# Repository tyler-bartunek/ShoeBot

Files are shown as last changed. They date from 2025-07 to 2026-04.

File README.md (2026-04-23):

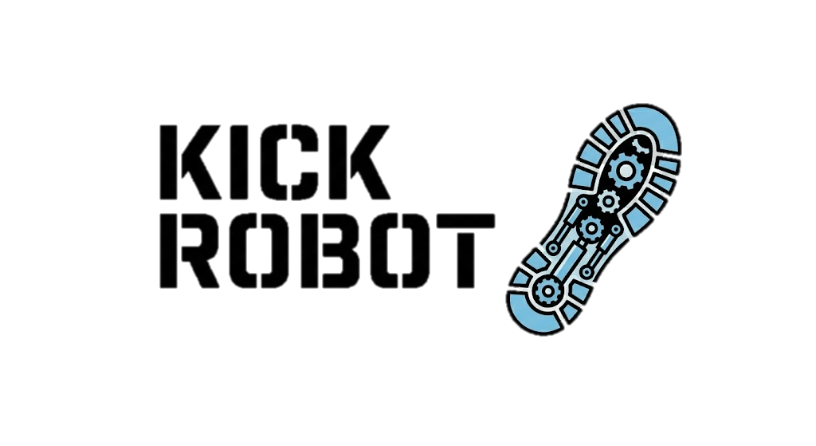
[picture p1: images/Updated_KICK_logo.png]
KICK Logo
# The KICK Robot 

&nbsp;
&nbsp;
_Democratizing robotics, one shoebox at a time_

The KICK (Kinematically Interchangeable Control Kit) Robot framework is an open-source platform designed to make learning about and development of mobile robotic systems accessible, modular, and affordable.

## Table of Contents
- [Repository Structure](#repository-structure)
- [The Wiki](#the-wiki)
- [Module Descriptions](#module-descriptions)
- [Hardware](#hardware)
  - [Printed Components and Module Fit](#printed-components-and-module-fit)
- [Future development](#future-development)
- [FAQ](#faq)
- [License](#license)

## Repository Structure
- `/hardware/` – STL and STEP files for 3D printing
- `/software/` – Code for the centralized controller (in progress), example firmware for modules, and hardware test scripts
- `/docs/` – Printing instructions, and additional reference material as it becomes available (PDF)
- `/images/` – Holds images used in this README, as well as some others throughout the repository
- `README.md` – You are here.

## The Wiki
Documentation for this project, including: 

- Part orientation and printer setting recommendations
- Assembly instructions
- Calibration and hardware validation protocols
- System-level descriptions
- and more

are being migrated to the [project wiki](https://www.github.com/tyler-bartunek/KICK-Robot/wiki) for ease of access
and navigation purposes. There's a lot that goes into this system, and it is only fitting that worthy documentation
would be quite extensive, requiring a wiki to track it all. 

## Module Descriptions
Here are a few of the modules under development at present for the KICK Robot. Once these modules are fully fleshed
out, a homebrew guide will be produced and added to the wiki.

1. Wheels: This module consists of DC motors and mecanum wheels, represents minimal functional example (systems integration in process).
2. Shoeshine: Offers quadrupedal motion through use of servomotors (Pending Initial Design)
3. HexaBox: Requires six mounts, offers six-legged locomotion through use of servomotors. (Pending Initial Design)

## Hardware

### Printed Components and Module Fit
Both STEP and STL files for all components to be printed are provided under the hardware directory, with directions for
the base hardware and wheels module provided in the wiki. As modules are added, printing directions specific
to those modules will be added. This system was prototyped using an Ender 3 V2 and Cura slicer using 
PLA+, with dimensions set to reflect typical tolerances for that printer with the intent of clearance fits with minimal play between 
mounting rails and modules.

## Future development
This project is still under development, and additional details such as component IDs, synchronization, and timing
requirements will be made available as they are validated 

## FAQ

1. Why shoeboxes?

>I had originally set out to make what essentially amounts to just the wheels module as a CAD and mechatronic portfolio piece.
Seeking to understand the design considerations, I started to immerse myself in literature surrounding mecanum wheel devices 
and discovered something that is in hindsight self-evident: different design decisions like the wheel spacing and orientation 
fundamentally alters the dynamics of the system and therefore influence control. Creating modular systems to explore the impact 
of these parameters was largely underexplored in what I found, so I set out to make my own. But I needed a good frame. Something
cheap and easy to deploy. As I looked around me, I saw an unused shoebox. And the KICK Robot was born. 

>Realistically any cardboard box will work, but at the time a shoebox seemed like the right size for what I set out to accomplish.

2. Why didn't you use \<insert fastener here\> to fasten the modules to the box?

>In the early days, I explored a number of different means for mounting the hardware to the box. The current design for mounting
hardware to the box solves two problems simultaneously: the first is that of establishing a secure connection with minimal
assembly complexity, the second is offering a path for routing the wires from inside the box to the modules on the outside.

3. Doesn't the act of cutting into the box limit the reusability of a single box to test multiple design parameters?

>Yes, as do other adhesives that have enough strength to reliably anchor the hardware to the outside of the box. 

## License
As of 19 November, 2025, this project is licensed under the terms of the [Apache License-2.0](LICENSE). Software provided prior 
to this date was licensed under the terms of the MIT license, and includes the content of the directory 
`/software/Hardware Characterization/Wheels Module`. The transition to the Apache License-2.0 is to reflect that this repository
contains more than just software. 

This project also uses PyMC in the motor characterization code for the Wheels module. PyMC is also licensed under the terms
of the [Apache License-2.0](LICENSE), and also includes software licensed under the MIT license. A notice is provided in the
main directory of this repository, to underline this point and include the necessary copy of the MIT license for portions 
covered by that license.

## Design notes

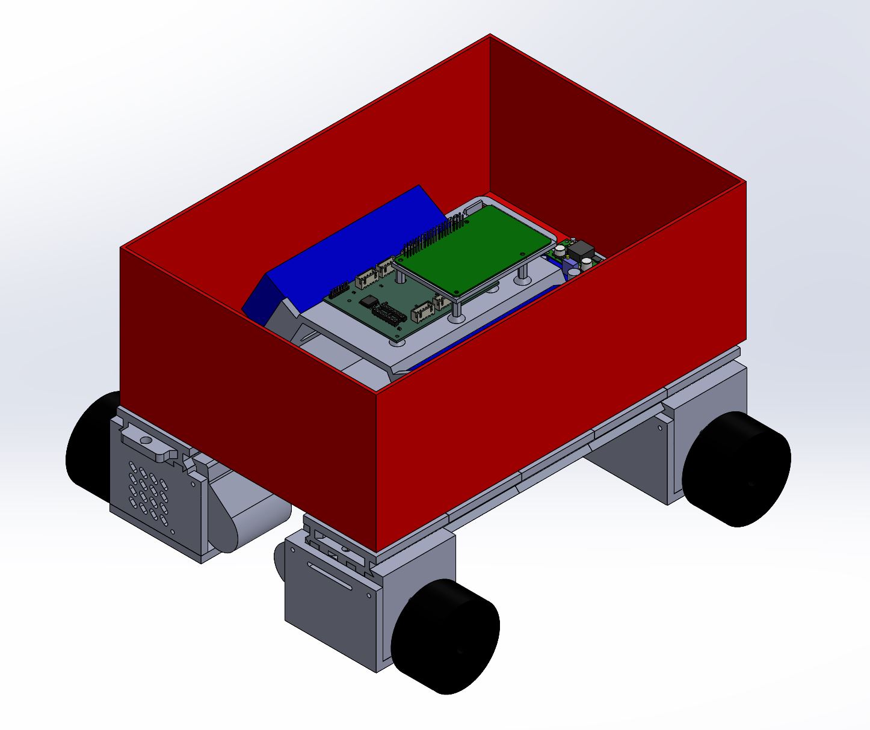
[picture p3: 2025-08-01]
images/ShoeBot_Wheels_Render_Iso.JPG

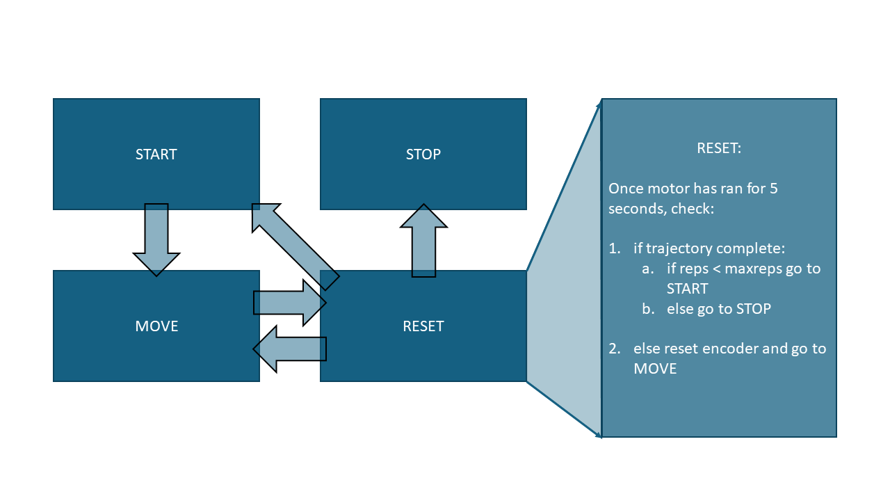
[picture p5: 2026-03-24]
images/wiki/MotorStateMachine.png

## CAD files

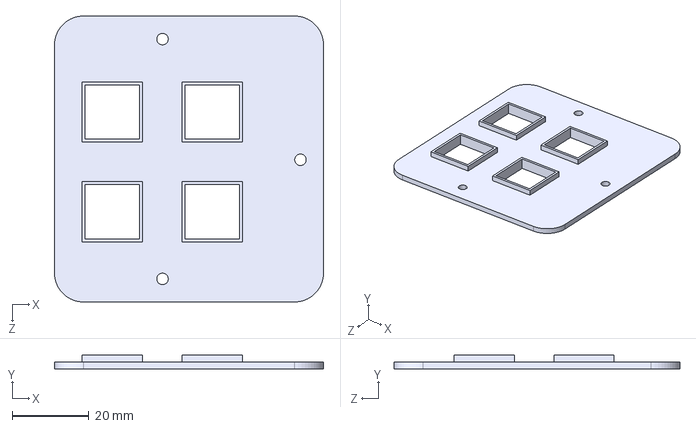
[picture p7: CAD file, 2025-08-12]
Hardware/Attachment Points/STEPs/BasePlate_Ext_Middle.STEP
70.0 x 3.60 x 74.4 mm

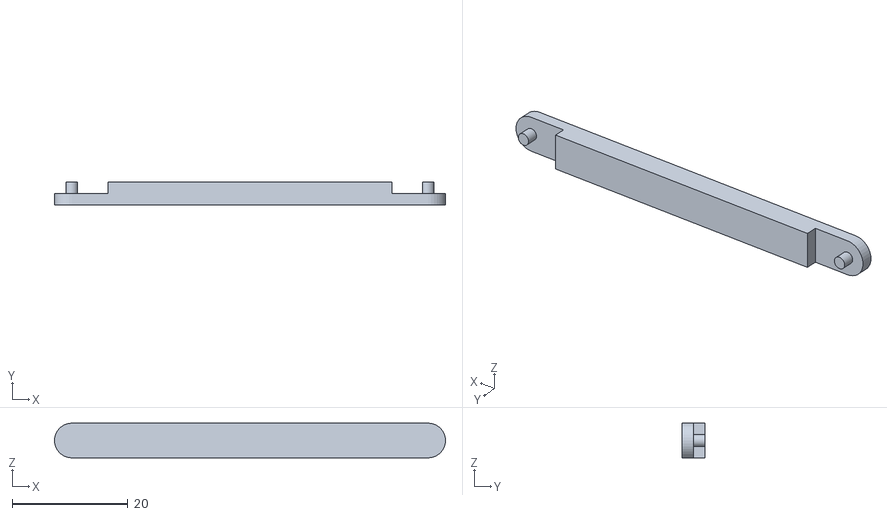
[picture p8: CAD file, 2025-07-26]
Hardware/Attachment Points/STLs/PlateSpacer.STL
67.5 x 4.00 x 6.00

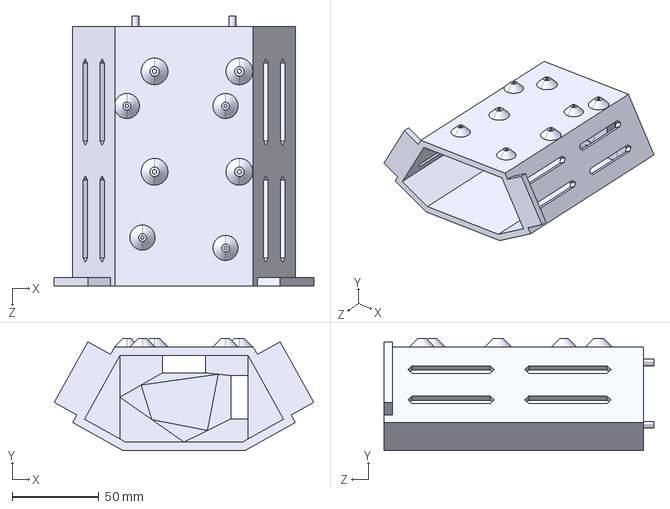
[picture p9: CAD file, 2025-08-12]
Hardware/Central Electronic Mounts/STEPs/Central_Electronics_Mount.STEP
150.0 x 65.0 x 156.0 mm

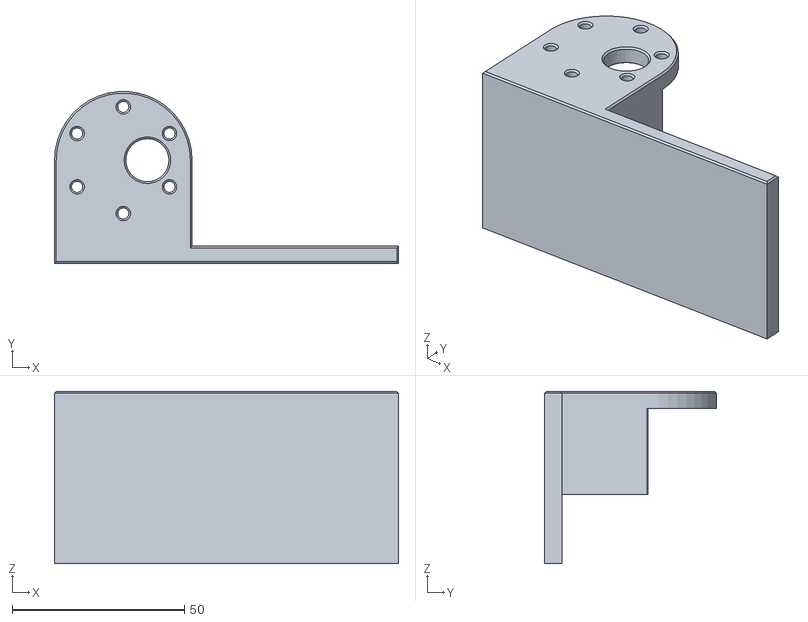
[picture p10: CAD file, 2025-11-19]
Hardware/Wheel Module/Motor Characterizetion STL/MotorWheel_Characterization.STL
100.0 x 49.9 x 50.0

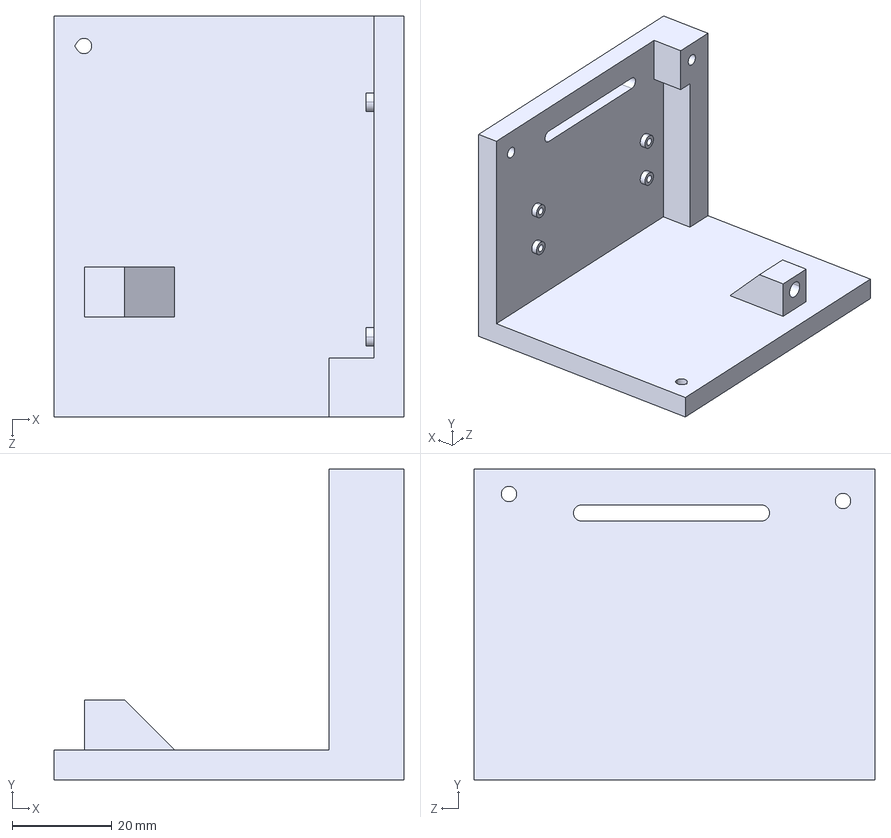
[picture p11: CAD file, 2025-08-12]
Hardware/Wheel Module/STEPs/Motor_Mount_Side_Bottom.STEP
70.0 x 62.2 x 80.2 mm

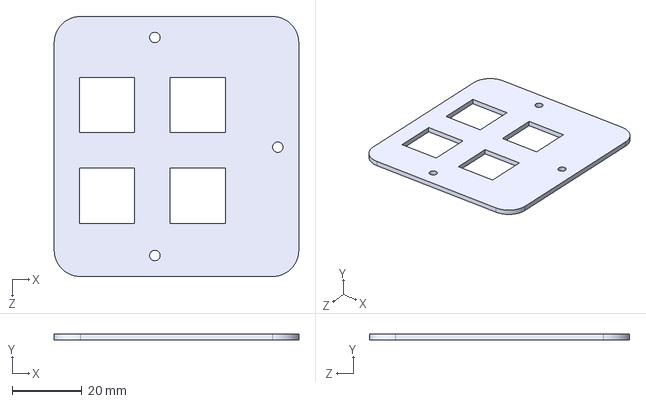
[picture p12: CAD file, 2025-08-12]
Hardware/Attachment Points/STEPs/BasePlate_Int_Middle.STEP
70.0 x 1.80 x 74.4 mm

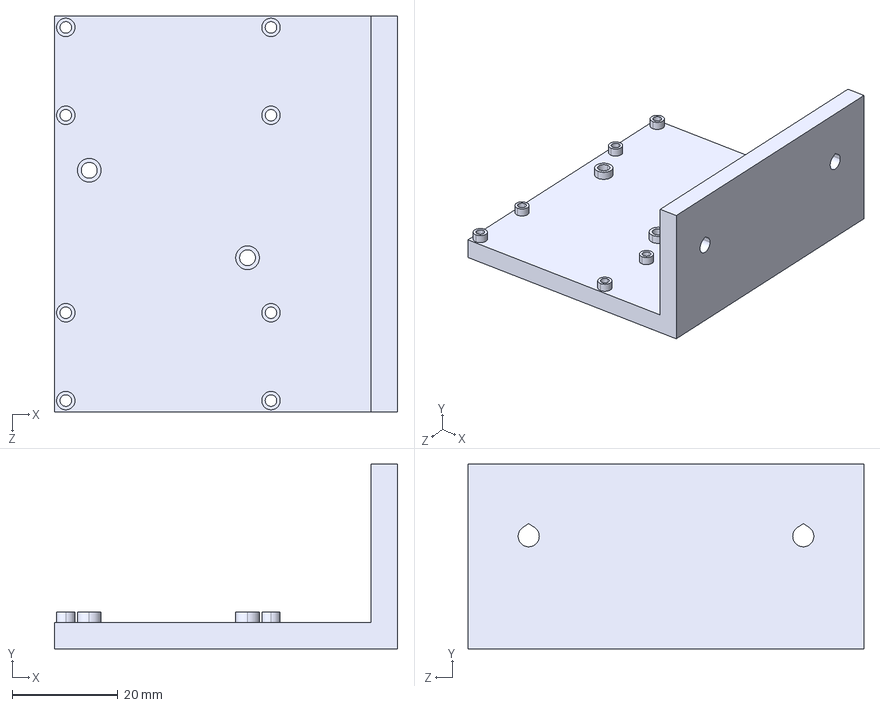
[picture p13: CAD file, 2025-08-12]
Hardware/Central Electronic Mounts/STEPs/Buck_Mount.STEP
65.0 x 35.0 x 75.0 mm

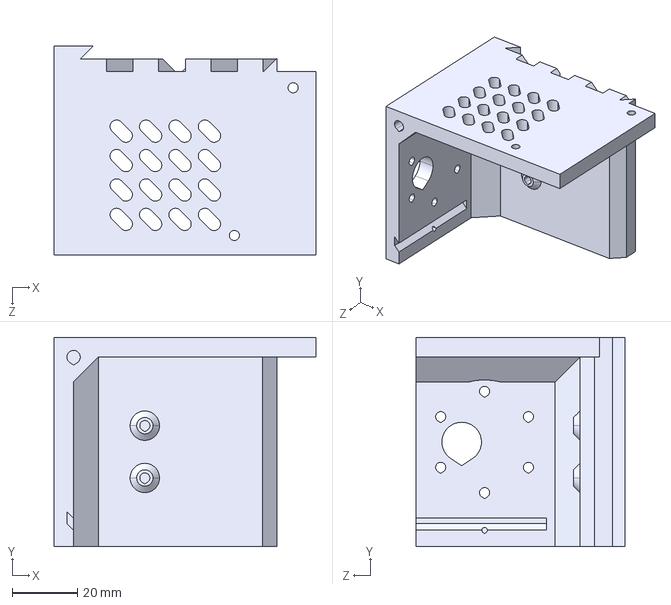
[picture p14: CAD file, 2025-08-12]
Hardware/Wheel Module/STEPs/Motor_Mount_Attachment.STEP
80.2 x 64.0 x 64.0 mm

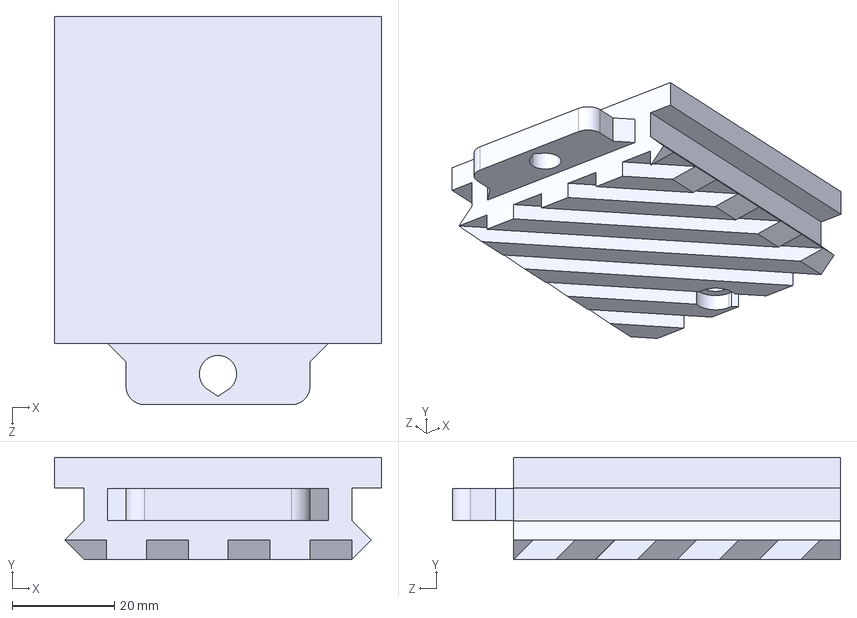
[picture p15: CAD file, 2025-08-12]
Hardware/Attachment Points/STEPs/BaseMount.STEP
64.0 x 20.0 x 76.0 mm

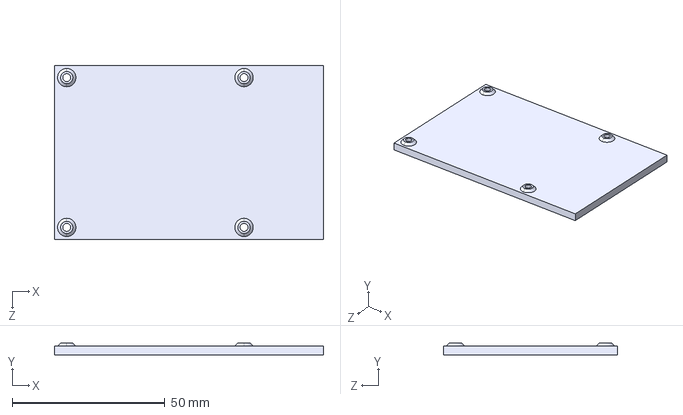
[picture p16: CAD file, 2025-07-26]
Hardware/Central Electronic Mounts/STEPs/Rpi_3b_mount.STEP
88.0 x 4.00 x 57.0 mm

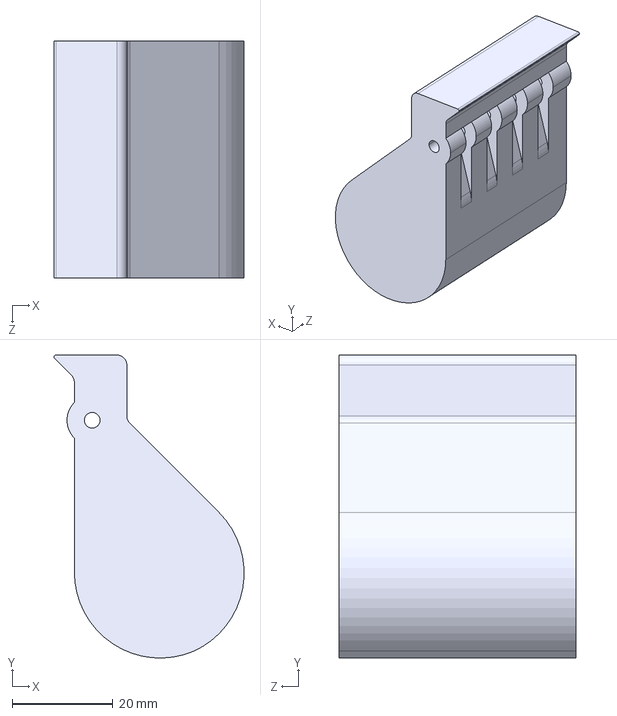
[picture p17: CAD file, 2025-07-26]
Hardware/Wheel Module/STEPs/Handle.STEP
37.6 x 60.1 x 47.0 mm

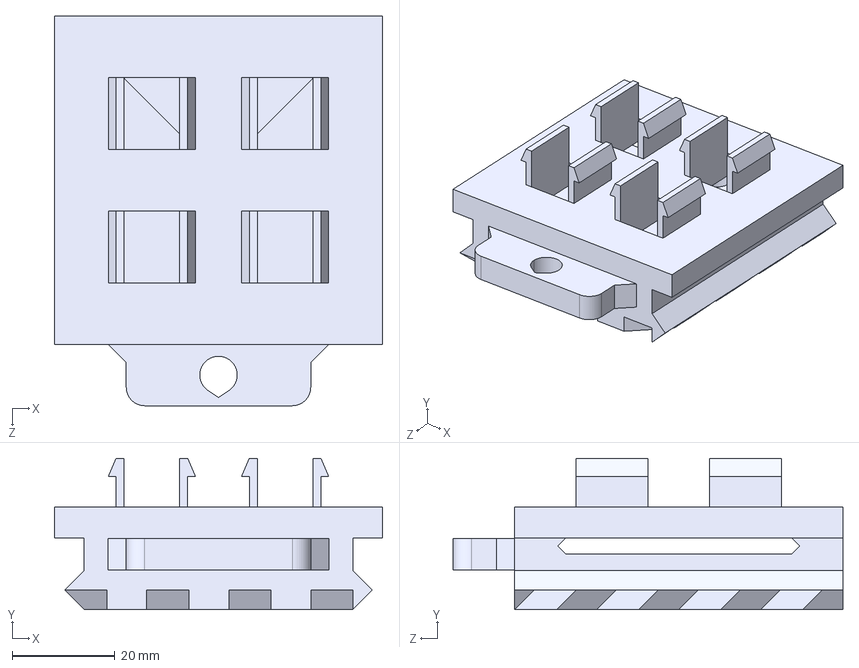
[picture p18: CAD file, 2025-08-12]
Hardware/Attachment Points/STEPs/BaseMount_Clips.STEP
64.0 x 29.5 x 76.0 mm

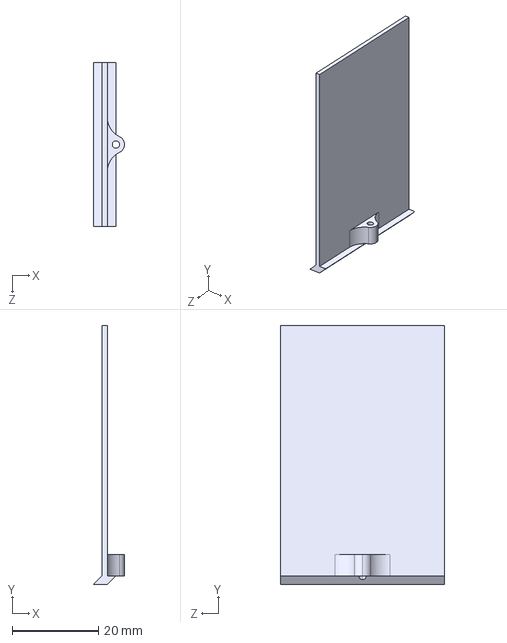
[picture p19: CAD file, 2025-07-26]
Hardware/Wheel Module/STEPs/Pico_Shield.STEP
7.20 x 60.0 x 38.0 mm

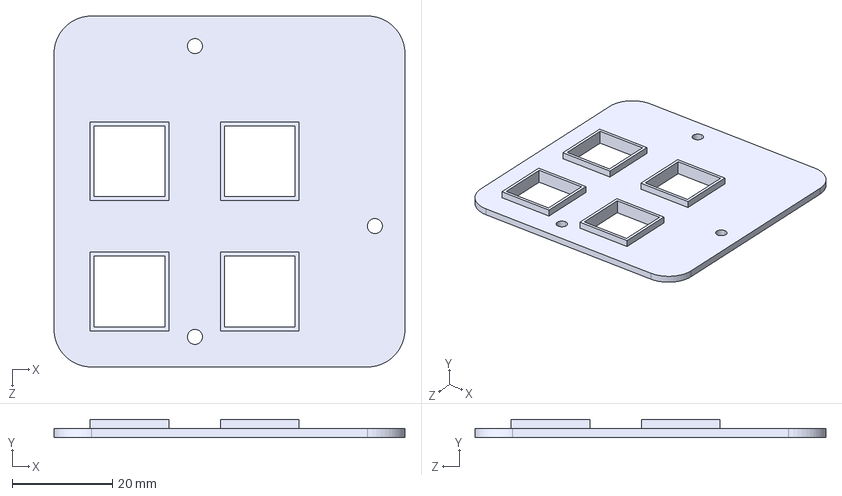
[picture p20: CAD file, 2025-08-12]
Hardware/Attachment Points/STEPs/BasePlate_Ext_Corner.STEP
70.0 x 3.60 x 70.0 mm

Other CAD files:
Hardware/Attachment Points/STEPs/BasePlate_Int_Corner.STEP
Hardware/Attachment Points/STLs/BaseMount.STL
Hardware/Attachment Points/STLs/BaseMount_Clips.STL
Hardware/Attachment Points/STLs/BasePlate_Ext_Corner.STL
Hardware/Attachment Points/STLs/BasePlate_Ext_Middle.STL
Hardware/Attachment Points/STLs/BasePlate_Int_Corner.STL
Hardware/Attachment Points/STLs/BasePlate_Int_Middle.STL
Hardware/Central Electronic Mounts/STLs/Central_Electronics_Mount.STL
Hardware/Central Electronic Mounts/STLs/Rpi_3b_mount.STL
Hardware/Wheel Module/STLs/Handle.STL
Hardware/Wheel Module/STLs/MotorMount_Attachment.STL
Hardware/Wheel Module/STLs/Motor_Mount_Attachment.STL
Hardware/Wheel Module/STLs/Motor_Mount_Side_Bottom.STL
Hardware/Wheel Module/STLs/Pico_Shield.STL

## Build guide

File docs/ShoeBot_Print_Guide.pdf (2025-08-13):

# ShoeBot

# Quick-Start Excerpt: Printing Guide

## Revision Date: August 7, 2025

# Contents

## Downloading Files

These instructions are written for a Windows 10 computer, though the basic principles should transfer reasonably well to other platforms like Mac and Linux operating systems.

## Installing Git

Open a web browser and navigate to https://git-scm.com/ and go to the downloads page. Follow their posted directions, and once installation is complete you will be ready to get started.

## Cloning the Repository

Once git is installed, open a terminal and navigate to the directory where you would like to save the project files. If you know how to do this already, you can skip the steps detailing this process.

### Navigating to Desired Directory using Command Prompt

You do this on Windows by going to the search bar and typing “cmd”, you should see something like the following come up, though the specifics will depend on the software you have installed on your device.

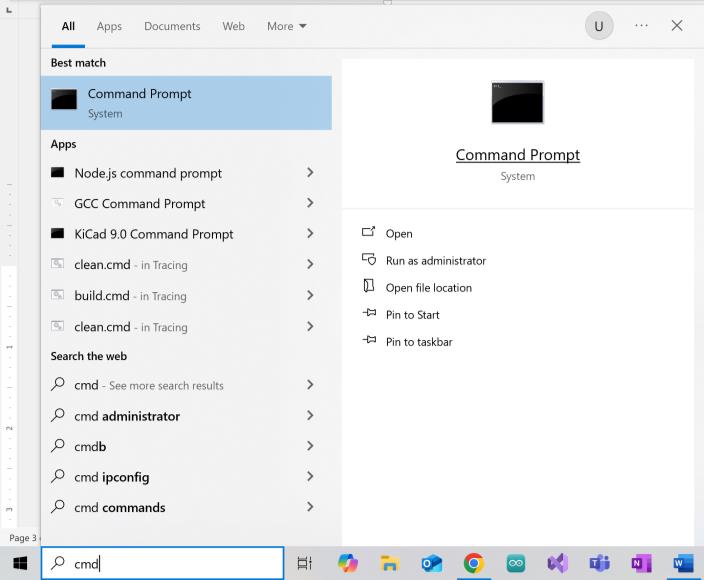
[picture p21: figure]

Figure 1. This screenshot illustrates opening the Command Prompt terminal from the Windows search bar.

1. Open Command Prompt and you should see a terminal window open. Odds are good that your desired location is going to be somewhere off the user directory, which is what Command Prompt opens to by default. In this example, the desired directory is a desktop folder created specifically for the user’s GitHub repositories.

2. Type cd ./<name of target directory> In the example provided in Figure 2, the full command is cd ./Desktop/My Stuffs/Git Repos/

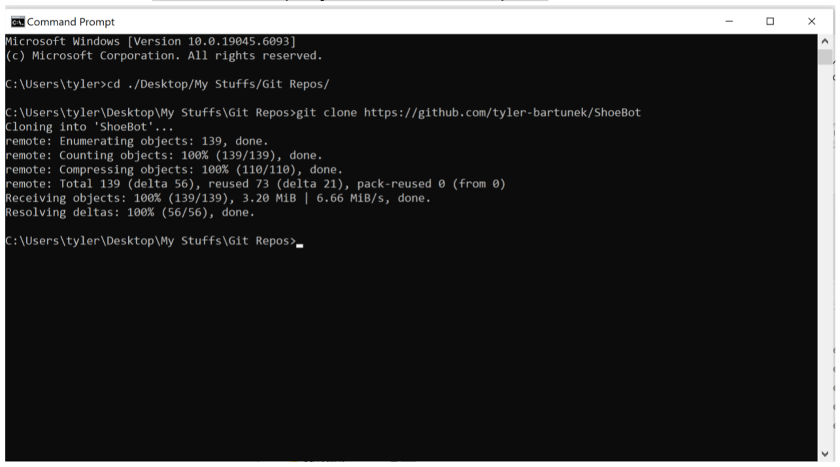
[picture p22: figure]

Figure 2. The complete set of commands necessary to get a clone of the repository onto your local device.

### Finally Cloning the Repository

Now that you are set up with git and are have navigated to the location you want the files to download, it is time to download a copy of the files into this location. Type or copy-paste

git clone https://github.com/tyler-bartunek/ShoeBot

into your terminal. The download process should run automatically and once finished you should have a new folder in that location named ShoeBot. Note that it may prompt you to sign in to github, which may entail setting up an account.

If this step has finished successfully, then you can now close the Command Prompt and continue navigation through the File Explorer like usual.

## Printing Instructions for Hardware

Navigate to the Hardware directory of the repository. In it, you will find folders for

- Attachment Points
- Central Electronic Mounts

- SPI Hub PCB KiCad files
- Wheel Module.

This section will concern all of these folders except the SPI Hub folder, as that information is for an optional component that is not 3D-printed. Every folder that has parts to be 3D-printed will contain folders for STEP and STL files, with the former provided in the event that you need to modify the base design of any of the components.

All parts were printed using PLA+ during the design process with:

- 0.4 mm nozzle and line width
- 20% infill (cubic)
- Tree supports as applicable
- 2 wall lines
- 50 mm/s print speed

To maximize print time efficiency, it is strongly recommended to print multiple components at once. For example, printing half of the rail pieces in a batch and all of the motor mount attachments in another batch instead of each rail and motor mount attachment piece individually. With these print settings it was not uncommon to encounter 2+ day prints on an Ender 3V2 running Marlin. So again, the recommendation is to print as many things simultaneously as possible.

In total, you will need to print the following to match the development setup:

- 6 Base Mount Clips
- 4 Base Mounts
- 4 Internal Corner Plates
- 2 Internal Middle Plates
- 4 External Corner Plates
- 2 External Middle Plates
- 4 Motor Mount Attachments
- 4 Motor Mount Side Bottoms
- 4 Handles
- 4 Pico Shields
- 1 Central Electronics Mount
- 1 Buck Converter Mount
- 1 Raspberry Pi 3b+ Mount
- 4 Spacers (print last)

For best results, print at a 0.1 mm layer height as this will allow in Cura for steeper overhangs and fewer supports.

## Attachment Points

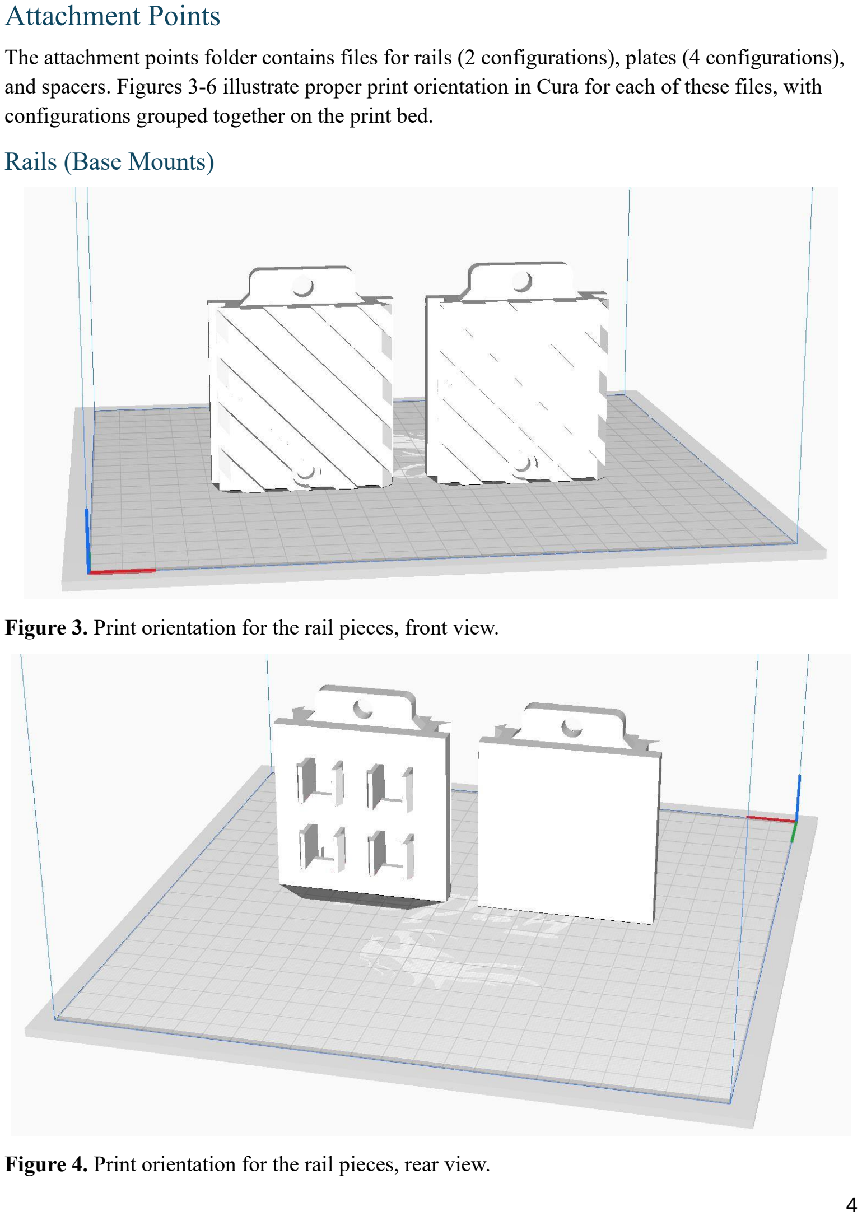
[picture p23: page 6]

The attachment points folder contains files for rails (2 configurations), plates (4 configurations), and spacers. Figures 3-6 illustrate proper print orientation in Cura for each of these files, with configurations grouped together on the print bed.

### Rails (Base Mounts)

Figure 3. Print orientation for the rail pieces, front view.

Figure 4. Print orientation for the rail pieces, rear view.

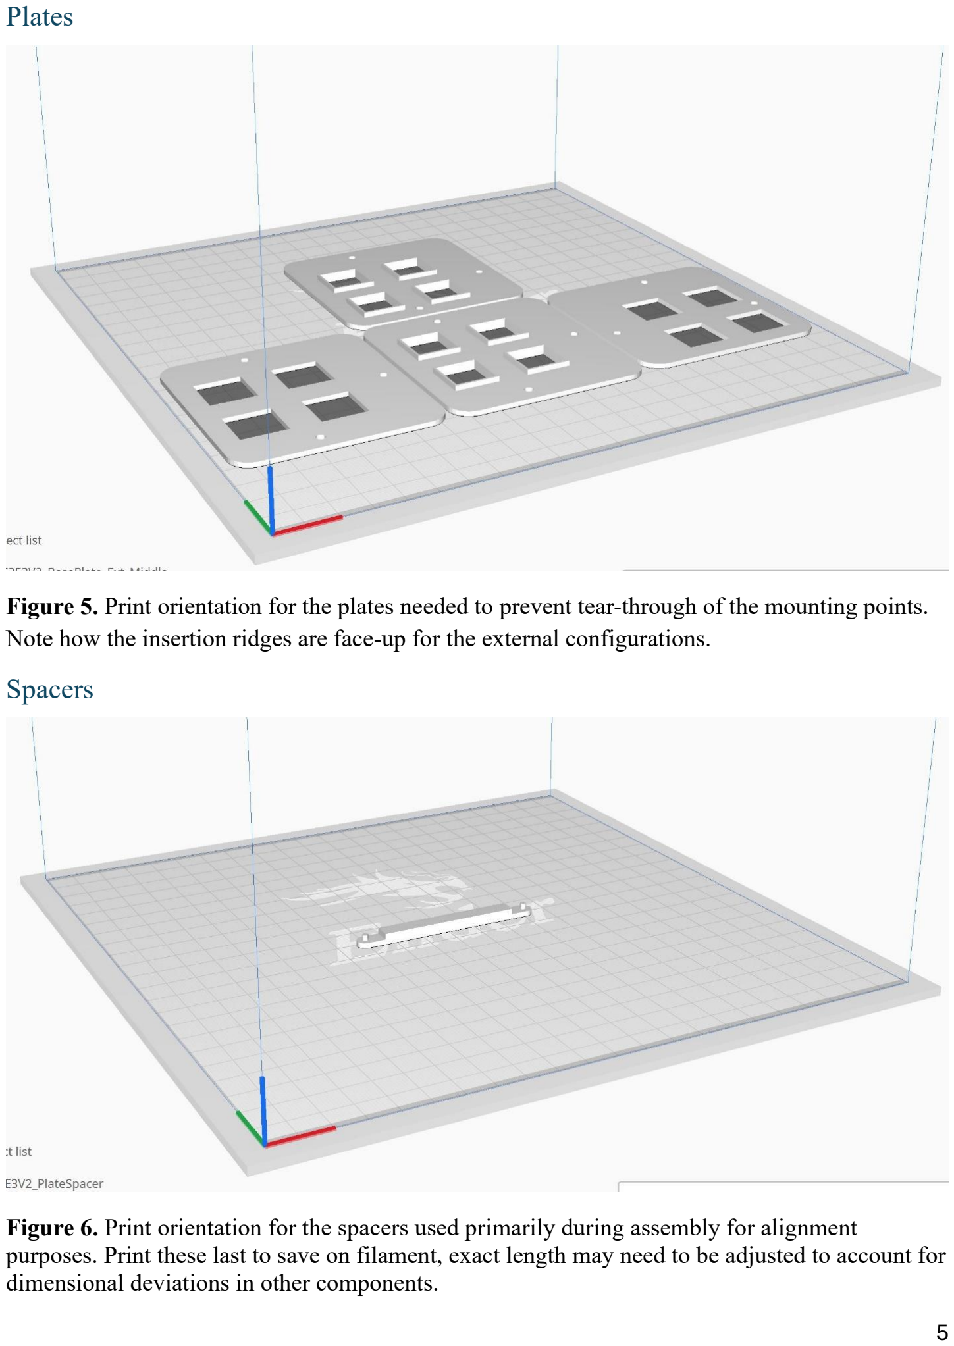
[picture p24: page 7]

### Plates

Figure 5. Print orientation for the plates needed to prevent tear-through of the mounting points. Note how the insertion ridges are face-up for the external configurations.

### Spacers

Figure 6. Print orientation for the spacers used primarily during assembly for alignment purposes. Print these last to save on filament, exact length may need to be adjusted to account for dimensional deviations in other components.

## Central Electronics Mounts

### Raspberry Pi 3B+ Mount

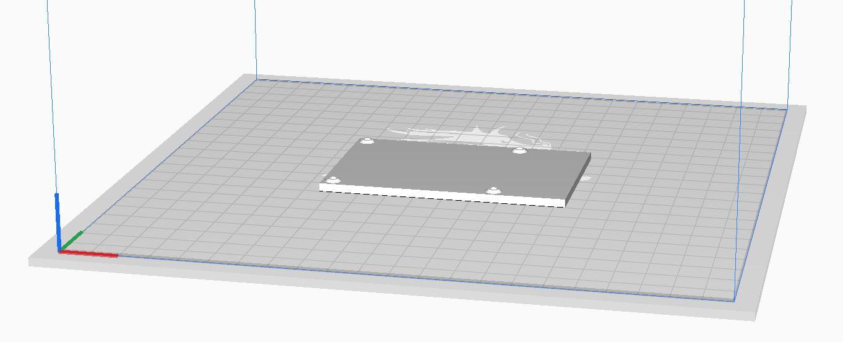
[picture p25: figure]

Figure 7. Print orientation for the plate that the raspberry pi sits upon, with screws going through the pi and this plate into standoffs.

### Central Mount

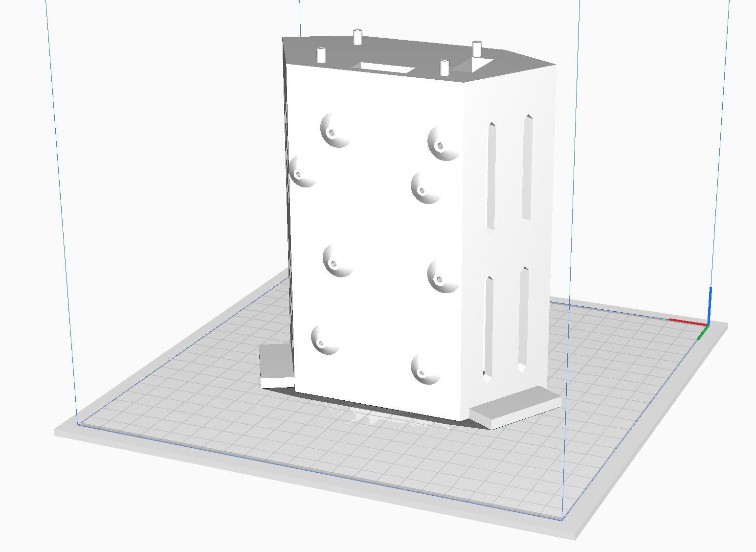
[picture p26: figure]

Figure 8. Print orientation for the central electronics mount. Note that the center of this will be hollow, and you may have to disable supports through part of it in order to improve print times. Small cuts were made in the top of the hollowed out portion to decrease the bridging distance to always be less than 50 mm.

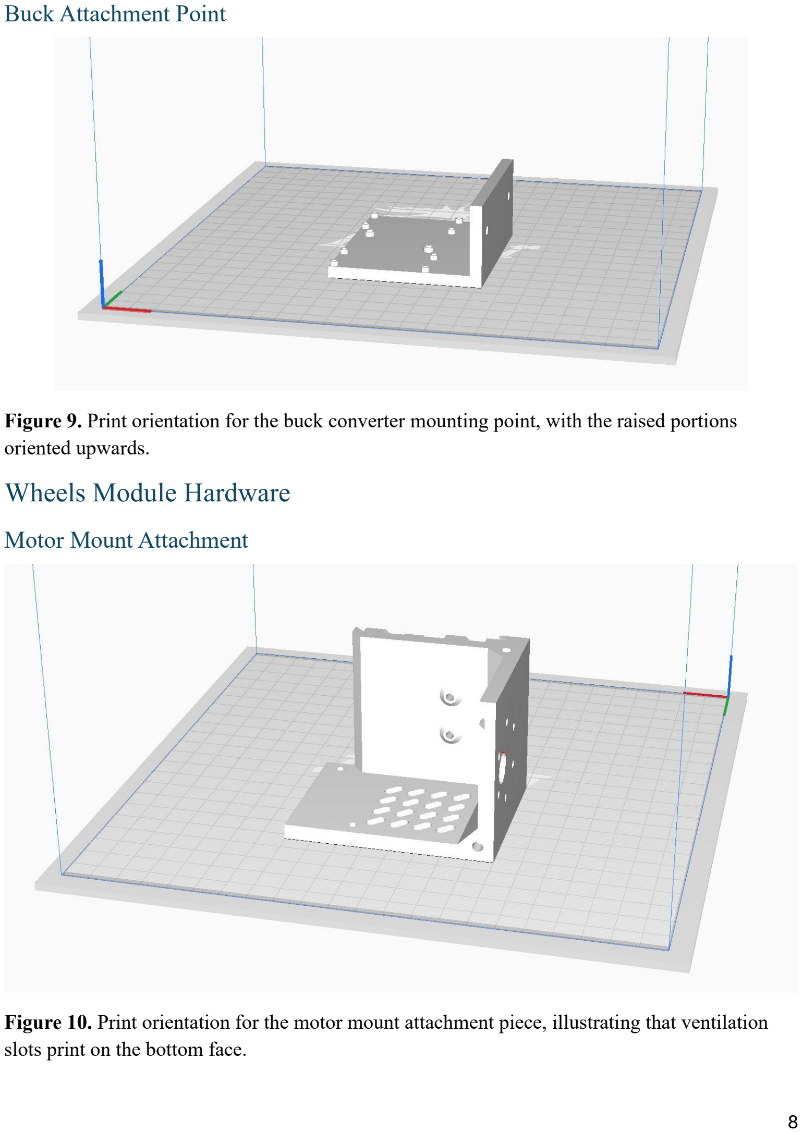
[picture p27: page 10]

### Buck Attachment Point

Figure 9. Print orientation for the buck converter mounting point, with the raised portions oriented upwards.

## Wheels Module Hardware

### Motor Mount Attachment

Figure 10. Print orientation for the motor mount attachment piece, illustrating that ventilation slots print on the bottom face.

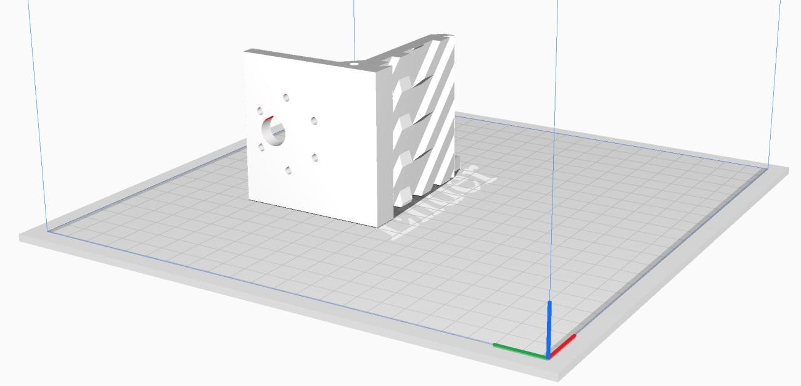
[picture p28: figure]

Figure 11. Secondary view of the print orientation for the motor mount attachment piece, showing that the teardrop shape for the motor attachment holes point upward and the way that the channels should appear in the correct print orientation.

### Motor Mount Side Bottom

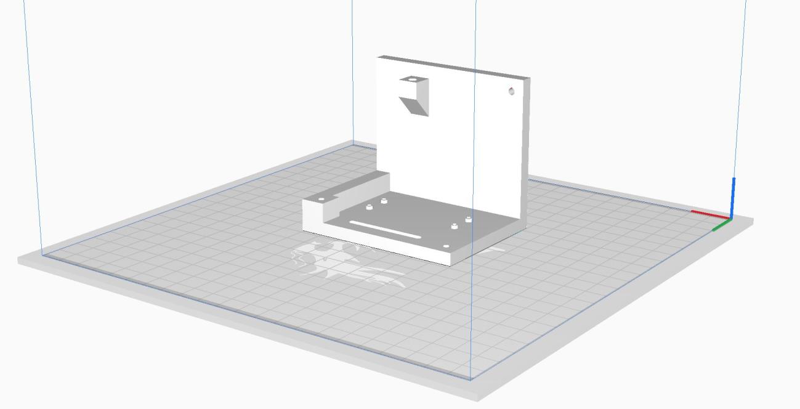
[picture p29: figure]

Figure 12. Print orientation for the bottom (and side) piece of the Wheels module enclosure. Note the direction of the teardrop shape for the hole in the top right corner, as well as how the chamfer plays a supporting role for another hole.

### Handle

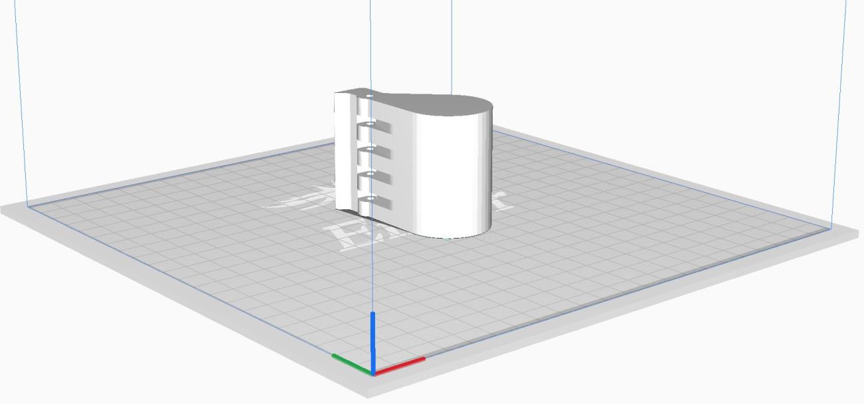
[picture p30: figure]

Figure 13. Print orientation for the handle of the wheels module. Note that care should be taken to ensure that the gaps for the springs are cleaned out well enough for the springs to fit, as supports will want to fill this space.

### Pico Shielding

Special consideration: this part is much taller than it is wide, and as such it is recommended to enable z-hop when printing this piece because there is a risk of the print failing due to the nozzle knocking it over.

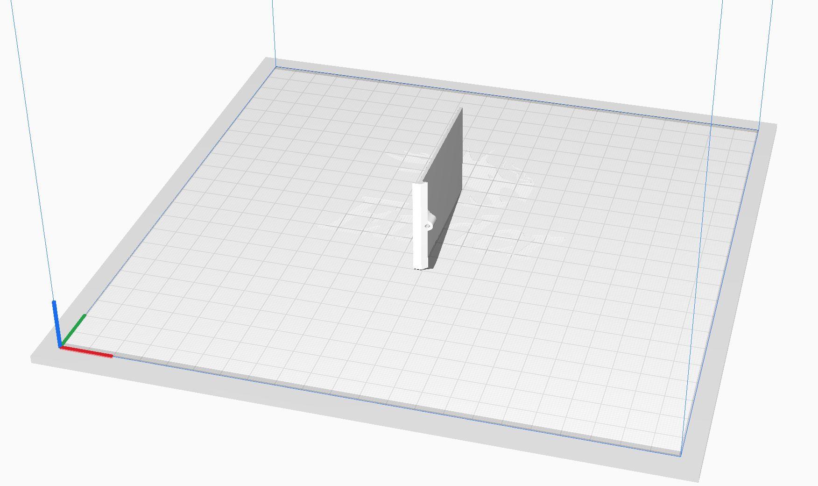
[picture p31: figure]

Figure 14. Print orientation for the Pico shielding piece. Note that, aside from fitting into the attachment piece (including the M1.6 screw hole) though, not a lot of dimensional accuracy is strictly necessary for this piece as it will just be backing for EMI shielding.

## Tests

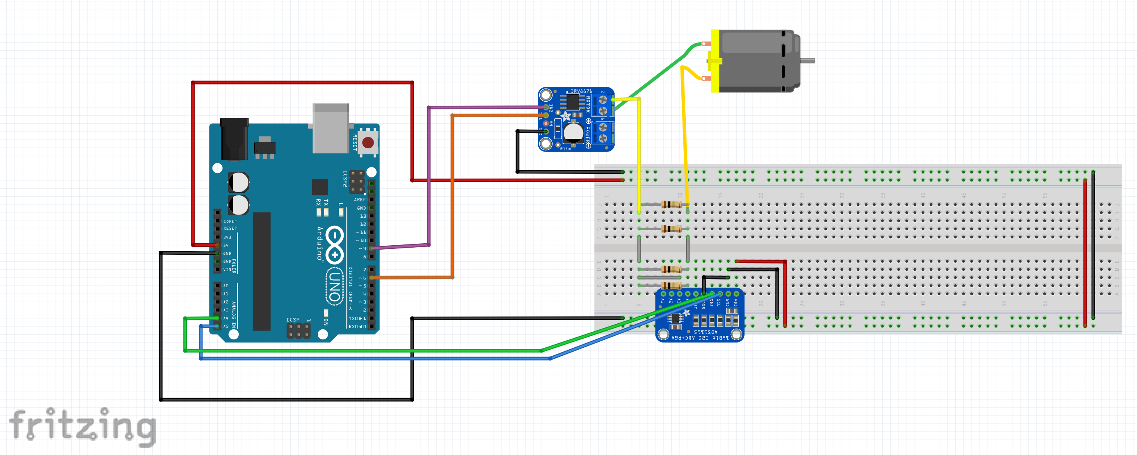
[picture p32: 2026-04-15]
images/wiki/motor_characterization_fritzing_diagram.png

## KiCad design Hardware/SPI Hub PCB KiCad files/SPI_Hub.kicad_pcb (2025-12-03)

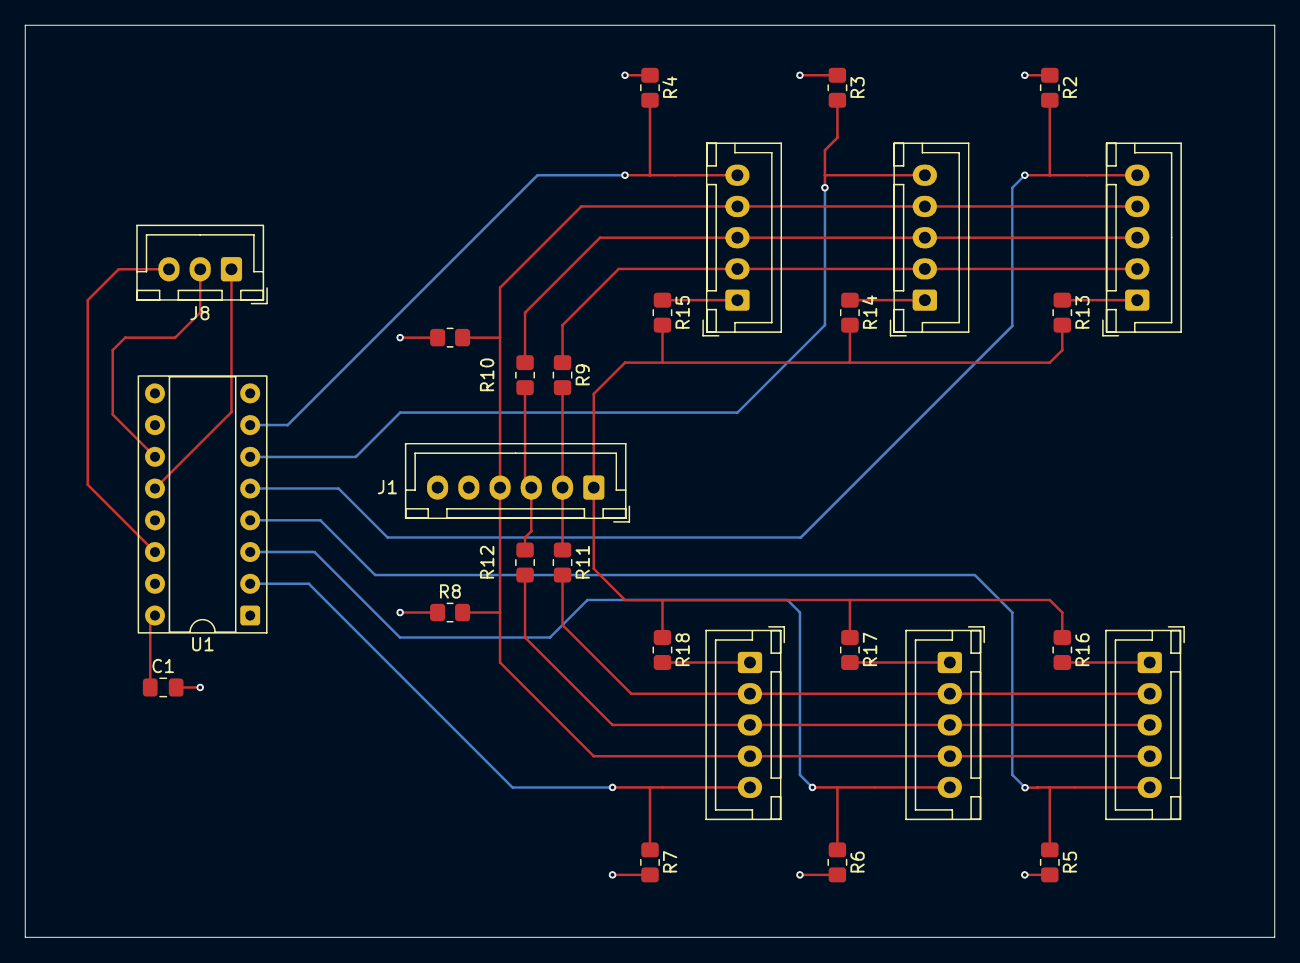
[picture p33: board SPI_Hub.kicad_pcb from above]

Board: 4 copper layers, 100.0 x 73.0 mm, 28 parts (0 on the bottom side), 25 nets.

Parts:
C1: 0.1 uF; C_0805_2012Metric_Pad1.18x1.45mm_HandSolder
J1: Conn_01x06_Socket; JST_XH_B6B-XH-A_1x06_P2.50mm_Vertical
J2: Left Front; JST_XH_B5B-XH-A_1x05_P2.50mm_Vertical
J3: Left Center; JST_XH_B5B-XH-A_1x05_P2.50mm_Vertical
J4: Left Rear; JST_XH_B5B-XH-A_1x05_P2.50mm_Vertical
J5: Right Front; JST_XH_B5B-XH-A_1x05_P2.50mm_Vertical
J6: Right Center; JST_XH_B5B-XH-A_1x05_P2.50mm_Vertical
J7: Right Rear; JST_XH_B5B-XH-A_1x05_P2.50mm_Vertical
J8: Conn_01x03_Socket; JST_XH_B3B-XH-A_1x03_P2.50mm_Vertical
R1, R2, R3, R4, R5, R6, R7, R8: 10k; R_0805_2012Metric_Pad1.20x1.40mm_HandSolder
R9, R10, R11, R12: 33; R_0805_2012Metric_Pad1.20x1.40mm_HandSolder
R13, R14, R15, R16, R17, R18: R; R_0805_2012Metric_Pad1.20x1.40mm_HandSolder
U1: 74AHC595; DIP-16_W7.62mm_Socket

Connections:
+3.3V: C1.1, J1.5, R1.1, R2.1, R3.1, R4.1, R5.2, R6.2, R7.2, R8.1, U1.10 (~SRCLR), U1.16 (VCC)
/CIPO: J1.1, R13.2, R14.2, R15.2, R16.1, R17.1, R18.1
/COPI: J2.2, J3.2, J4.2, R9.1
/DATA: J8.3, U1.14 (SER)
/LATCH: J8.1, U1.12 (RCLK)
/SCK: J2.3, J3.3, J4.3, R10.1
/SHCLK: J8.2, U1.11 (SRCLK)
/SYNC: J1.4, J2.4, J3.4, J4.4, J5.4, J6.4, J7.4, R1.2, R8.2
GND: C1.2, J1.6, U1.8 (GND), U1.13 (~OE)
unnamed: J1.2, R9.2, R11.1
unnamed: J1.3, R10.2, R12.1
unnamed: J2.1, R13.1
unnamed: J3.1, R14.1
unnamed: J4.1, R15.1
unnamed: J5.1, R16.2
unnamed: J5.2, J6.2, J7.2, R11.2
unnamed: J5.3, J6.3, J7.3, R12.2
unnamed: J6.1, R17.2
unnamed: J7.1, R18.2
cs1: J7.5, R7.1, U1.2 (QC)
cs2: J6.5, R6.1, U1.3 (QD)
cs3: J5.5, R5.1, U1.4 (QE)
cs4: J2.5, R2.2, U1.5 (QF)
cs5: J3.5, R3.2, U1.6 (QG)
cs6: J4.5, R4.2, U1.7 (QH)

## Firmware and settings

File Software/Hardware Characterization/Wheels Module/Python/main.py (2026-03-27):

"""
MotorCharacterize_SpeedBoost
"""

#Standard library imports: basic functionality
import os
import os.path as pth
import pandas as pd
import numpy as np

#Serial communication and post-processing
from SerialStreamParser import GatherAndStore
from PostProcessing import MotorData, ParseMotorData, ReshapeMotorData, GetTimesAndVoltages

#generating unique filename for date and time
from datetime import datetime

#MCMC code and simulations
from mcmc_simulator import HierarchicalModel, InitializeSimulations, RunBlocks, RunCommandForParams, PackOutputList
from StateModels import MotorModel

#Kalman Filter, MLE fitting
from filters import EWMA, StateObserver

#Plotting, as well as loading in trace data from MCMC
import matplotlib.pyplot as plt
import arviz as az 

#Set the random seed (done after bayesian and monte carlo fitting procedure)
np.random.seed(0)
    

#############################################################################################################################
############################################# Helper/Packing Functions ######################################################
#############################################################################################################################   


def WriteParamsToFile(param_dict:dict[str,float], file) -> None:
    for param in param_dict.keys():
        file.write("{} = {}\n".format(param, param_dict[param]))

    file.write("\n")

def OpenParamsFromFile(filename:str, param_keys:list[str]) -> tuple[dict[str, float], list[dict[str,float]]]:

    params_list_motors = []
    with open(filename, 'r') as file:

        chunks = file.read().split('\n\n')
        for chunk in chunks:
            lines = chunk.split('\n')

            params_dict = {param:0 for param in param_keys}

            for line in lines[1:]:

                key_value_separation = line.split(' = ')
                try:
                    params_dict[key_value_separation[0]] = float(key_value_separation[1].strip())
                except KeyError:
                    raise KeyError("Mismatch between expected keys and zeroth value of key_value_separation")

            if 'Motor' in lines[0]:
                params_list_motors.append(params_dict)
            
            elif 'Global' in lines[0]:
                global_params_dict = params_dict.copy()
            else:
                pass
    
    return global_params_dict, params_list_motors
                
            
#############################################################################################################################
######################################################## Main ###############################################################
#############################################################################################################################
def main():

    #Serial communication variables
    COM_PORT = "COM3"
    BAUD_RATE = 230400

    time_cutoff = 800 #Record for 800 seconds

    #File naming information, timestamps each file it creates to prevent accidental overwrites
    motor = 'C'
    block_number = 1
    date_info = datetime.now()
    mmddyyyy = "{}{}{}_{}{}".format(date_info.month, date_info.day, date_info.year,date_info.hour, date_info.minute)

    #First line is for general fitting data files, second for filter testing
    data_filename = "motor_data_romeo_Motor{}_Block_{}_{}".format(motor, block_number, mmddyyyy)
    # data_filename = "motor_data_romeo_Motor{}_{}".format(motor, mmddyyyy)

    #First line is for general fitting data files, second for filter testing
    data_folder = pth.join(pth.dirname(__file__), "data/RCBD_Trials")
    # data_folder = pth.join(pth.dirname(__file__), "data/Disturbance_Tests")

    #lists of commands, to be used in plotting and processing steps
    multi_speed_commands = [31, 63, 95, 127, 159, 191, 223, 255]

    #Flags that control what the program is doing: collecting data, providing early visualizations, or preprocessing data
    collecting_data = False
    plot_raw_data = False
    preprocess_data = False

    #Model identification
    mcmc_ready = False
    compute_nominal_params = False

    #Filter tuning 
    tune_filter = True

    if collecting_data:

        GatherAndStore(COM_PORT, BAUD_RATE, time_cutoff, data_filename)
        
    if plot_raw_data:

        multi_speed_files = os.listdir(data_folder)
        MultiData = [MotorData(cell, filepath=data_folder) for cell in multi_speed_files]

        #Plot time vs PWM and Run number for data to check if we are cycling through commands correctly
        MultiData[0].plot('Time','Position')
        plt.show()

    if preprocess_data:

        multi_speed_files = os.listdir(data_folder)
        MultiData = [MotorData(cell, filepath=data_folder) for cell in multi_speed_files]
        
        aggregated_data = ParseMotorData(MultiData, multi_speed_commands)

        aggregate_data_path = pth.join(pth.dirname(__file__), "data")
        aggregated_data.to_csv(pth.join(aggregate_data_path, "Aggregate_Motor_Data_RCBD.csv"), index = False)
    
    if mcmc_ready:

        #Load in the datset
        aggregate_data_path = pth.join(pth.dirname(__file__), "data")
        aggregated_data = pd.read_csv(pth.join(aggregate_data_path, "Aggregate_Motor_Data_RCBD.csv"))

        #Instantiate the model
        h_model = HierarchicalModel(aggregated_data)
        #Fit the model
        h_model.fit(sd_multiplier=3)

        #If the model ran without divergences, save result
        if h_model.trace.sample_stats['diverging'].sum() == 0:
            h_model.trace.to_netcdf("data/Accepted_trace.nc")

        #Summarize fitted model
        print(az.summary(h_model.trace, var_names=["R", "K", "b", "c", "J"], round_to = 4))
        print(az.summary(h_model.trace, var_names = ["R_m", "K_m", "b_m", "c_m", "J_m"]))

        #Trace plot
        az.plot_trace(h_model.trace, var_names = ["R", "K", "b", "c", "J"], legend=True)
        plt.show()

        #Plot pairs of group and motor parameters
        az.plot_pair(h_model.trace, var_names = ["R", "R_m"], kind="kde", divergences = True)
        az.plot_pair(h_model.trace, var_names = ["K", "K_m"], kind="kde", divergences = True)
        az.plot_pair(h_model.trace, var_names = ["b", "b_m"], kind="kde", divergences = True)
        az.plot_pair(h_model.trace, var_names = ["c", "c_m"], kind="kde", divergences = True)
        az.plot_pair(h_model.trace, var_names = ["J", "J_m"], kind="kde", divergences = True)
        plt.show()

    if compute_nominal_params:

        #Prepare to write the parameters to a file
        param_file = "data/parameters.txt"
        f = open(param_file, 'w')

        #Set the number of simulations and initialize
        num_sims = 100
        motors, blocks, runs, params_global, params_motor_list, MultiDataReshape = InitializeSimulations("data/Aggregate_Motor_Data_RCBD.csv",
                                                                                                         "data/Accepted_trace.nc", num_sims= num_sims)

        #Run through the motors and get simulations for each block at command 255
        command = 255
            
        #Instantiate global-level model
        global_model = MotorModel(params_global)

        global_idx_stack = []
        
        for id, motor in enumerate(motors):
            
            #Instantiate global-level model
            motor_model = MotorModel(params_motor_list[id])

            motor_ind_idx_stack = []

            models = [global_model, motor_model]

            print("Simulating motor {}".format(motor))
            f.write("Motor {}\n".format(motor))

            run_command = lambda global_out_stack, motor_out_stack, models, data, sr_values, run:RunCommandForParams(global_out_stack, motor_out_stack, models, data, sr_values, run, command)
            RunBlocks(global_idx_stack, motor_ind_idx_stack, models, motor, blocks, runs, MultiDataReshape, multi_speed_commands, run_command)

            best_motor_params = PackOutputList(motor_ind_idx_stack, for_params = True, dict_to_pattern = params_motor_list[id])
            WriteParamsToFile(best_motor_params, f)
            print("...done.")

        print("Simulations finished, no more motors.")
        global_params_dict = PackOutputList(global_idx_stack, for_params=True, dict_to_pattern = params_global)
        f.write("Global Model\n")
        WriteParamsToFile(global_params_dict, f)

        f.close()

    if tune_filter:

        #Load my global and motor-level parameters
        params_global, params_motor_list = OpenParamsFromFile("data/parameters.txt", ["R", "K", "b", "c", "J"])

        #Load in my test data
        data_folder = pth.join(pth.dirname(__file__), "data/Disturbance_Tests")
        test_data = [MotorData(cell, filepath = data_folder) for cell in os.listdir(data_folder)]

        #Define the motor labels, and number of runs
        motors = ['A', 'B', 'C', 'D']
        runs = list(range(1,6))

        #Reshape my motor test data into a dict
        test_data_reshape = {motor:[] for motor in motors}
        for data in test_data:
            filename_segmented = data.filename.split('_')
            motor_label = filename_segmented[3][-1]
            if motor_label in motors:
                test_data_reshape[motor_label].append(data)


        #Create the filepath for the observer data plot figures to go
        #Filepath(s) for saving plots
        plot_path = pth.join(pth.dirname(__file__), "filter plots")
        speed_plot_path = pth.join(plot_path, "speed")

        #make the path if it doesn't exist
        if not pth.exists(plot_path):
            #Specifically make the path to position vs speed data
            os.mkdir(plot_path)
            os.mkdir(speed_plot_path)

        #Instantiate the filter
        alpha = 0.01 #filter gain, higher numbers indicate more trust in new measurements
        filter = EWMA(alpha)

        for run in runs:

            for command in multi_speed_commands:

                #Create subplots with labels, appropriate size (10x7 inches)
                fig_speed, ax_speed = plt.subplots(2,2)
                fig_speed.set_size_inches(10,7) 

                #Set overall title
                fig_speed.suptitle("Speeds for Run = {}, Command = {} \n alpha = {}".format(run, command, alpha))

                for id, motor in enumerate(motors):

                    row_idx = id // 2
                    col_idx = id - (row_idx * 2)

                    sr_values = test_data_reshape[motor][0].get_step_windows(multi_speed_commands)

                    #Extract observed_states
                    times = sr_values[run][command]['Time'].values
                    positions = sr_values[run][command]['Position'].values
                    speed_init_compute = np.diff(positions) / np.diff(times)
                    speeds = np.concatenate([[0], speed_init_compute])

                    #Set title
                    ax_speed[row_idx, col_idx].set_title(motor)

                    #Enable grid lines
                    ax_speed[row_idx, col_idx].grid(True)

                    #Set x and y labels on outside edge
                    if col_idx == 0:
                        ax_speed[row_idx, col_idx].set_ylabel('Speed (rad/s)')
                    if row_idx == 1:
                        ax_speed[row_idx, col_idx].set_xlabel('Time (s)')

                    #Plot observed values
                    ax_speed[row_idx, col_idx].plot(times, speeds, label = "Observed")

                    #Make predictions
                    predictions = filter.predict_batch(speeds)

                    #Plot predicted values
                    ax_speed[row_idx, col_idx].plot(times, predictions, label = "Filter")
            
            #Create legend, removing duplicate labels
            handles, labels = plt.gca().get_legend_handles_labels()
            by_label = dict(zip(labels, handles))
            fig_speed.legend(by_label.values(), by_label.keys())

            #Save figure, plot results. Start by replacing decimals in gains with underscores
            speed_filename = "Speed_Plot_Run_{}_PWM_{}_alpha{}.jpg".format(run, command, alpha)
            fig_speed.savefig(pth.join(speed_plot_path, speed_filename))

            plt.show()


if __name__ == "__main__":

    main()

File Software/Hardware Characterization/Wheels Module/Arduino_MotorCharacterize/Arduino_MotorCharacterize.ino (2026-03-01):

/*
Sketch name: Romeo_MotorCharacterize.ino
Author: Tyler Bartunek
Purpose/Function: To collect data on the relationship between PWM command and speed.

Update as of September 19 2025: Moved some helper functions into header files and added use of templates
*/

//#define and #include
#include "Encoder.h"
#include "Wire.h"
#include "ADS1115_WE.h"
#include "Headers/SerialComms.h"
#include "Headers/Trajectory.h"
#include "Headers/Utils.h"

//Motor constants
#define GEAR_RATIO 19.0      //Reduction ratio of 1:19 (1 turn of output to 19 turns of input)
#define COUNTS_PER_REV 44.0  //11 pulses per revolution, quadrature encoding

//Hardware pins
#define MOTOR_IN1 6
#define MOTOR_IN2 9
#define ENC_A 2
#define ENC_B 3

//I2C Address:ADDR pin left floating
#define ADC_I2C_ADDR 0x48

//Encoder object
Encoder MotorEncoder = Encoder(ENC_A, ENC_B);

//ADC Object
ADS1115_WE adc = ADS1115_WE(ADC_I2C_ADDR);

//Commands being sent
int availableCommands[8] = { 31, 63, 95, 127, 159, 191, 223, 255 };

//Timing variables
unsigned long startTime = 0;  //Time that the setup completed, ms


void setup() {
  //Serial: set baud rate
  Serial.begin(230400);

  //I2C: Get wire going
  Wire.begin();

  //Set the direction pin mode
  pinMode(MOTOR_IN1, OUTPUT);
  pinMode(MOTOR_IN2, OUTPUT);

  //Set the counts appropriately
  MotorEncoder.write(0);

  //Start the ADC, get settings configured
  if (!adc.init()) {
    Serial.println("Fault state of ADC");  //Hopefully this doesn't awaken something
  }

  //Set appropriate gain, fastest rate, continuous mode to compare A0 and A1
  adc.setVoltageRange_mV(ADS1115_RANGE_0256); //Theoretically we could see as much as 556 mV, realistically more like 78
  //Options: 6144, 4096, 2048, 1024, 0512, 0256
  adc.setMeasureMode(ADS1115_CONTINUOUS);
  adc.setCompareChannels_nonblock(ADS1115_COMP_0_1); //Advised if we want non-blocking
  adc.setConvRate(ADS1115_860_SPS);

  bool started = false;  //Flag for keeping track of if we've started data acquisition

  //Await input from the Python script
  while (!started) {
    if (Serial.available() > 4) {
      String readyMessage = Serial.readStringUntil('\n');
      readyMessage.trim();
      if (readyMessage == "Ready") {
        Serial.println("Ready");
        started = true;
      }
    }
  }

  //Start the clock(s)
  startTime = millis();
}



void loop() {
  // put your main code here, to run repeatedly:

  //Trajectory and data structs initialized
  static Trajectory traj;
  static TestData data;

  //Flags
  static bool sending = true;
  static bool receiving = false;

  //Get the motor command, drive the motor (optional)
  data.motorCommand = GetTrajectory(traj, data);
  //Comment if not driving motor
  DriveMotor(data.motorCommand);

  //Get the current time and the time since the previous reading
  data.time = (millis() - startTime);

  if (HasElapsed(data.time, 2)) {  //Get and print readings every 2 ms

    //Read the encoder value: radians
    float reading = 2 * PI * MotorEncoder.read() / (COUNTS_PER_REV * GEAR_RATIO);
    data.position = long(reading * 100);

    //Read the current
    float currentFloat = adc.getResult_V() / .2609938;  //Dividing by shunt resistance
    data.current = long(currentFloat * 100);

    //We'll start with a Serial print, move on to a Serial write if necessary.
    if (sending) {
      SendData(data, 0xFA, 0xF8);
      sending = false;
      receiving = true;
    }
    if (receiving) {
      if (CheckReceived(0xFF)) {
        sending = true;
        receiving = false;
      }
    }
  }
}

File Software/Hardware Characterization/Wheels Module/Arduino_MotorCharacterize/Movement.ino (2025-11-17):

void DriveMotor(int command) {
  /*
Drives motor according to DRV8871 datasheet,
with 0 representing assumed braking and 255 representing 
full speed ahead. 

Note that we toggle the direction by pulling one of
the inputs high. This is so when the other input goes
high, we enter the braking regime; when the other input
goes low we move in the intended direction. This is the
recommended approach by the datasheet for PWM operation.
*/
  if (command > 0) {  //Forward
    digitalWrite(MOTOR_IN1, HIGH);
    analogWrite(MOTOR_IN2, 255-abs(command)); //Motor driver does opposite, forward when low and break when high
  } else if (command == 0) {  //Brake
    digitalWrite(MOTOR_IN1, HIGH);
    digitalWrite(MOTOR_IN2, HIGH);
  } else {  //Reverse
    digitalWrite(MOTOR_IN2, HIGH);
    analogWrite(MOTOR_IN1, 255-abs(command));
  }
}

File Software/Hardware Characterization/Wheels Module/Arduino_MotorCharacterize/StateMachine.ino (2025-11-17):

int GetTrajectory(Trajectory &traj, TestData &data) {

  //Initialize output
  static int command = 0;
  static int newCommand = 0;
  int maxReplicates = 5;
  int sizeCommandArray = sizeof(availableCommands) / sizeof(availableCommands[0]);

  switch (traj.state) {

    case START:
      
      shuffleArray(availableCommands, sizeCommandArray);
      newCommand = availableCommands[0];
      traj.lastChangeTime = millis();
      traj.state = MOVE;

      break;

    case MOVE:

      command = newCommand;

      if (HasElapsed(traj.lastChangeTime, 15000)) {  //Wait 15 seconds before changing command value
        newCommand = GetNextCommand(traj, data, availableCommands, sizeCommandArray);
        traj.state = RESET;
      }

      break;

    case RESET:

      command = 0;

      if (HasElapsed(traj.lastChangeTime, 5000)){

        if (!traj.finished){
          MotorEncoder.write(0);
          traj.state = MOVE;
        }
        else{
          if (data.runNumber <= maxReplicates) {
          traj.finished = false;
          MotorEncoder.write(0);
          traj.state = START;
        } else {
          traj.state = STOP;
        }
        }
      }

      break;

    case STOP:
      command = 0;
  }

  return command;
}

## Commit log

2025-07-25 Added frame-related step files
    [BaseMount.STEP, BaseMount_Clips.STEP, BasePlate_Ext_Corner.STEP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]
2025-07-26 Reorganized existing STEP files, added Wheel Module 3.5
    [BaseMount.STEP, BaseMount_Clips.STEP, BasePlate_Ext_Corner.STEP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]
2025-07-26 Adding PCB files and STL files for parts printed as well as motor mounts about to be printed
    [BasePlate_Ext_Corner.STL, BasePlate_Ext_Middle.STL, BasePlate_Int_Corner.STL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]
2025-08-07 Add image directory, STLs
    [BaseMount.STL, BaseMount_Clips.STL, Handle.STL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]
2025-08-12 Updated teardrop shapes, added central electronics STEP and STL
    [BaseMount.STEP, BaseMount.STL, BaseMount_Clips.STEP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]
2025-08-13 Updated KiCad schematic, tied unused Schmitt input to gnd
    [SPI_Hub.kicad_pcb, SPI_Hub.kicad_sch]
2025-08-13 Added print guide to docs, Updated README
2025-11-11 Revise chip select values and PCB assumptions
    Updated chip select values for active-low configuration and clarified PCB assumptions.
2025-11-17 Revise README for module updates and remove info in the wiki
    Removed sections on custom PCB and software communication protocols. Updated module descriptions with pending design notes.
2025-11-17 Enhance README with extended repo tagline.
    Added description of the ShoeBot framework to README.
2025-11-17 Revise module descriptions and printing directions
    Updated README to reflect changes in module descriptions and printing directions.
2025-11-17 Fixed STL file, added motor diagram
    [BaseMount.STL, BaseMount_Clips.STL, MotorMount_Attachment.STL]
2025-11-17 Adding initial pass at characterization code, fix later
    [Arduino_MotorCharacterize.ino, Movement.ino, PostProcessing.py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]
2025-11-19 Added bench test STL, removed extra py files
    [MotorWheel_Characterization.STL]
2025-11-20 Added current SPI fanout schematic image
2025-11-20 Add CMake and KiCad related files to .gitignore
2025-12-03 Updated and simplified PCB design
    [SPI_Hub.kicad_pcb, SPI_Hub_Rev0.kicad_sch]
2026-01-27 Initial attempt at general pico hardware cppf files
2026-03-01 improved project stuctures for motor characterization code
2026-03-01 Restructured motor characterization code folder
2026-03-04 built custom packages, pymc import fails due to deprecated scipy
    [mcmc_core.py]
2026-03-25 Adding pigpio test code for hub board
2026-03-27 Flattened packages to workspace root in motor characterization, installs work now
2026-03-27 Added requirements for motor characterization code
2026-04-05 Update README with software status and module details
    Clarify the status of the centralized controller and update module description for Wheels.
2026-04-15 Add fritzing diagram for motor characterization
2026-04-21 Refactor and patch pico code to scale better and use SYNC correctly
    [Module.cpp, SPITools.cpp, main.cpp]
